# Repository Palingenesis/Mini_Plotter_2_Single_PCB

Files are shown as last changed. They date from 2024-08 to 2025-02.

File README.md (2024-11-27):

# This is My Mini Plotter 2 with a Single PCB  
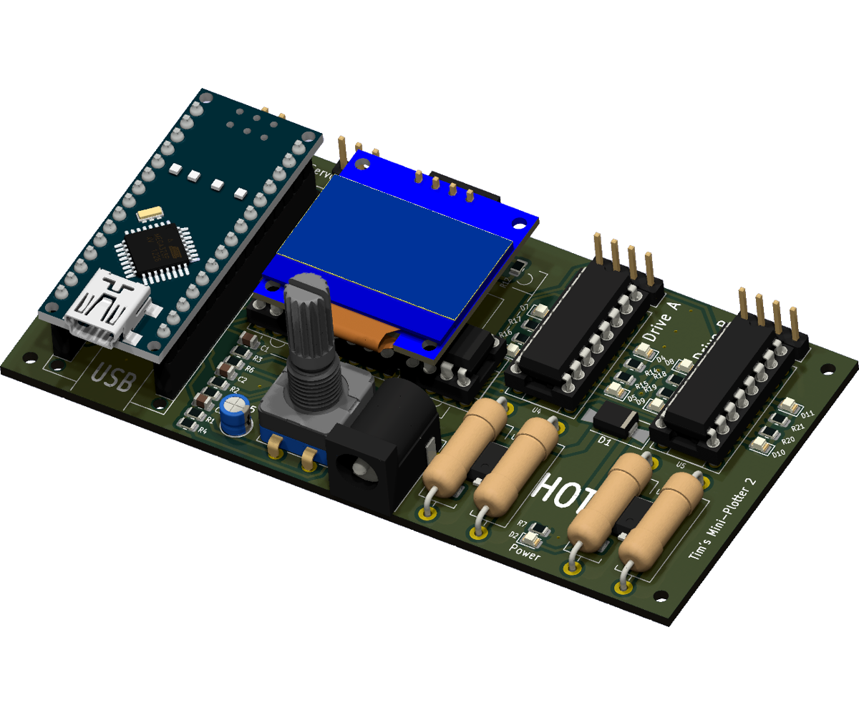
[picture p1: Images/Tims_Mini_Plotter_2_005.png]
  
## This is a Board to control two basic bipolar stepper motors.  
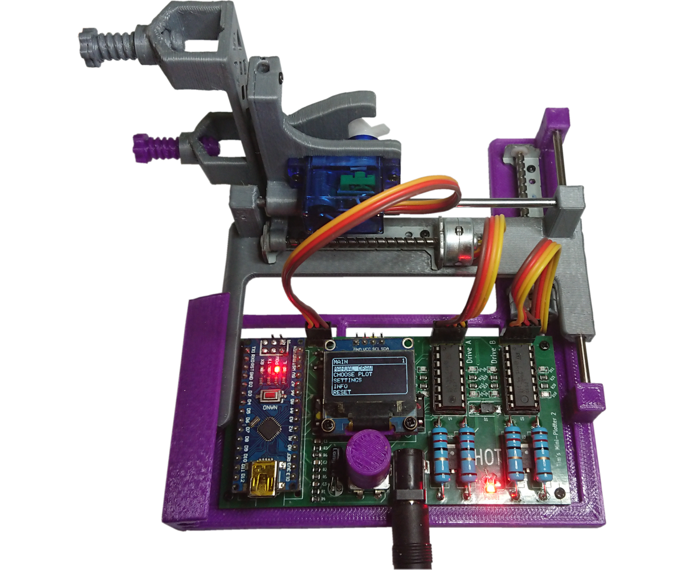
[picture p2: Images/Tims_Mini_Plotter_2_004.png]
Mini Plotter
  
## *The Board fitted to the Mini Plotter.*  
### Files for [KiCAD EDA](https://www.kicad.org/)  
There is [<span style="font-size: large;">**"Mini Plotter 2 Full.kicad_pcb.zip"**</span>](bom/) file  
* This can be used when **"Plot Files"** asked for at 
<sub></sub> 
when ordering 10 PCBs for $5  
* If you have <span style="font-size: large;">**[KiCAD EDA](https://www.kicad.org/)**</span>,  
<sub></sub>
have a Plugin Plugin that will make things simple to order a PCB,  
just load this project into <span style="font-size: large;">**[KiCAD EDA](https://www.kicad.org/)**</span> install the plugin click the Icon Plugin and it will create all the nesesery files needed and take you to order a PCB 
and compeate the form on 
<sub></sub> 
web site.  
  
<a href="https://www.pcbway.com/project/shareproject/Tim_s_Mini_Plotter_2_ec46c4f8.html">PCB from PCBWay</a>

### Files for [3D Printing](https://www.pcbway.com/rapid-prototyping/manufacture/?type=2&reffercode=TOP)  
There is [a folder with all the STL files needed](STL/) to print the Mini Plotter.

## Note!
The BOM only contains the Components for the Board.  
Other Parts required are:  
* Arduino Nano Module.
* 2 Stepper Motor 15mm dia. x 50mm Screw. (The type from CD or DVD drive)
* SG90 Servo.
* 3 lengths of 3mm Linear Rod.
* A light Spring 3mm x 25mm.
* 11 M1.7 x 6mm self tap flat nose screws.
* The 3D printed parts.
## About  
This is a PCBWay PCB Version of mini plotter I did quit a while ago, my original mini plotter I made of standard modules I bought and a home made PCB.

Details of the original can be found at my Blog here: [Tim's Mini Plotter 2 (tims-mini-plotter2.blogspot.com)](https://tims-mini-plotter2.blogspot.com/2019/01/tims-mini-plotter-2-this-is-new-project.html)

So it is the PCBWay PCB version.  
PCBWay do a great offer in prototyping PCBs, so I decided to make a version based around a single PCB.  
This is the same as the original except for the electronics, it has been made slightly longer to accommodate a single PCB.
## My Brief
For this project, I wanted to make a compact portable plotter using 2 motors from CD/DVD Drives.  
I wanted to use the cheap L298 drivers.  
I wanted to give it some memory where it can store some plots, and have a menu system to set some basic settings and be able to chose plots stored in memory.
## What I use
I use [FreeCAD](https://www.freecad.org/)  to design my 3D Prints, and [KiCAD EDA](https://www.kicad.org/) to design my PCB.  
Both these programs can integrate with each other. They are open source and I recommend them.  
[KiCAD EDA](https://www.kicad.org/) also has a plugin Plugin from <sub></sub> that makes it simple to order PCBs.
## History
My previous Mini Plotter Ver. 1 looked like this: [Version 1](https://tims-mini-plotter-1.blogspot.com/) [Version 1.3](https://www.youtube.com/watch?v=I_yTPbJcGrc&feature=youtu.be)
### Here is is a video of the original Mini Plotter 2 to show how it works.
*Click this image to see a video of it in use.*
[](https://www.youtube.com/watch?v=dSBTWS-KP68)
This new version works exactly in the same way.
## Stepper Motors
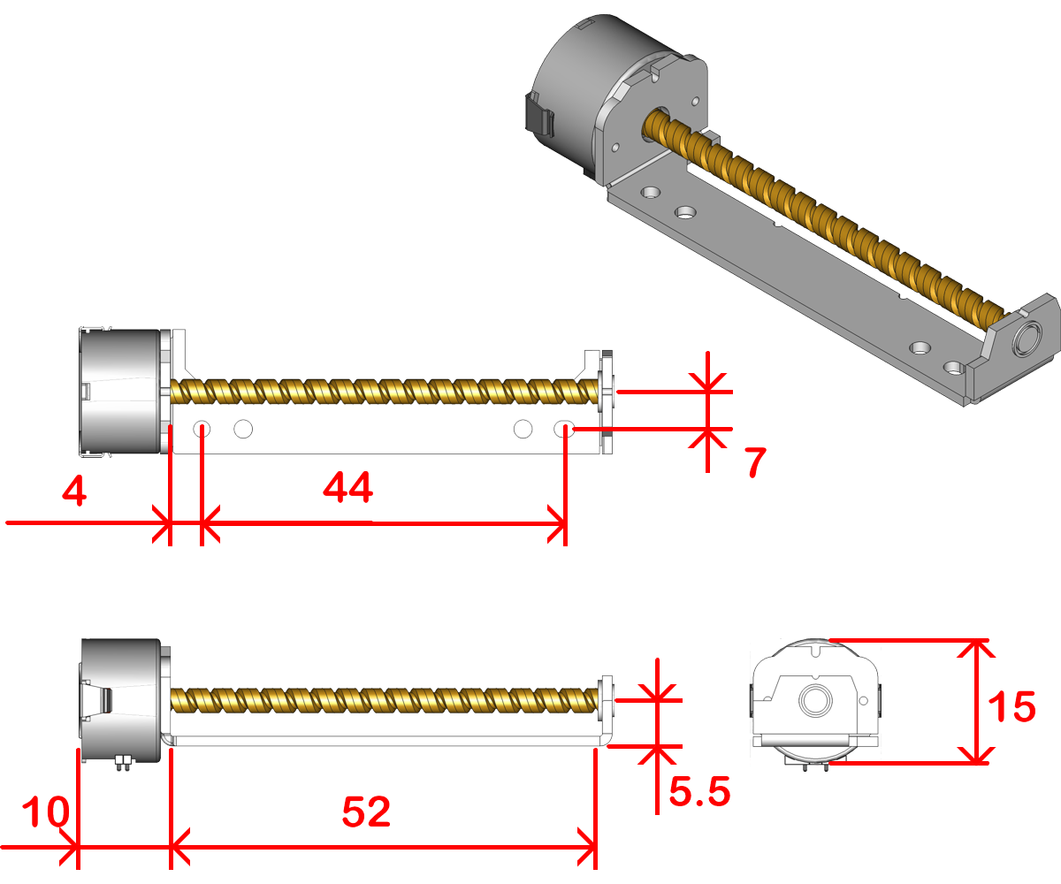
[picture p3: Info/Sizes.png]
  
The stepper motors I am using for this project are motors I repurposed from some CD/DVD drives.  
The dimensions are approximate, I have put holes to suit what I have shown.  
Care should be taken when soldering new cables to these motors, it is very easy to melt the coil bobbins.  
The only data I could find for these type of motors was from a data sheet for a PL15S-020. (I will assume other makes are similar)  
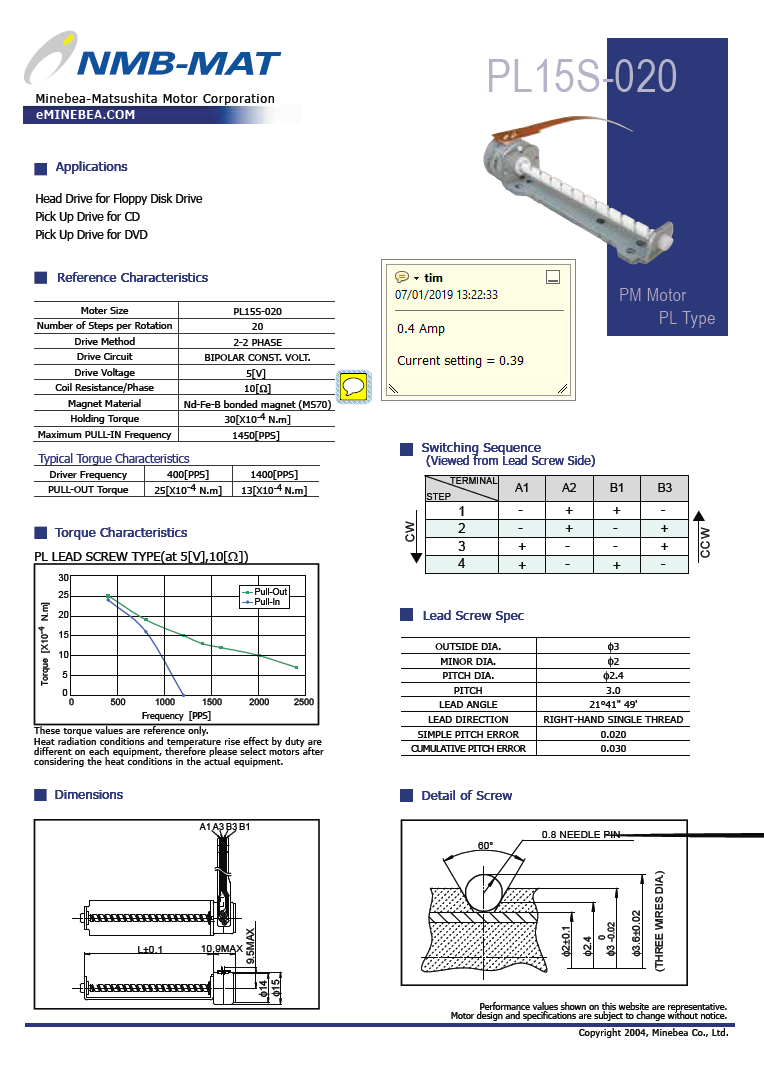
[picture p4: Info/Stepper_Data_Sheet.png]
  
If we do a little maths: V=ri, 5 volt divided by 10 ohms = 0.5 Amps  
As I could check the resistance of my motors and found them to have 12 ohm resistance.  
I will work on the assumption mine require 0.4A. (5/12=0.42A)  
They probably are designed to take 0.5A, but: they are normally mounted to a large metal frame that acts like a massive heat sink.  
My steppers are going to be mounted to plastic. (PLA)  
Knowing this I will be wiring the Voltage regulators in the Constant Current configuration. (see L78xx family data sheets)  
I had some 12.5 ohm 2 Watt Resistors, so I have 2 for each drive.  
12.5 ohm 2 Watt two in parallel making 6.25 ohm.  
## Motor Driver
I have used two L293 drivers to drive the stepper motors.  
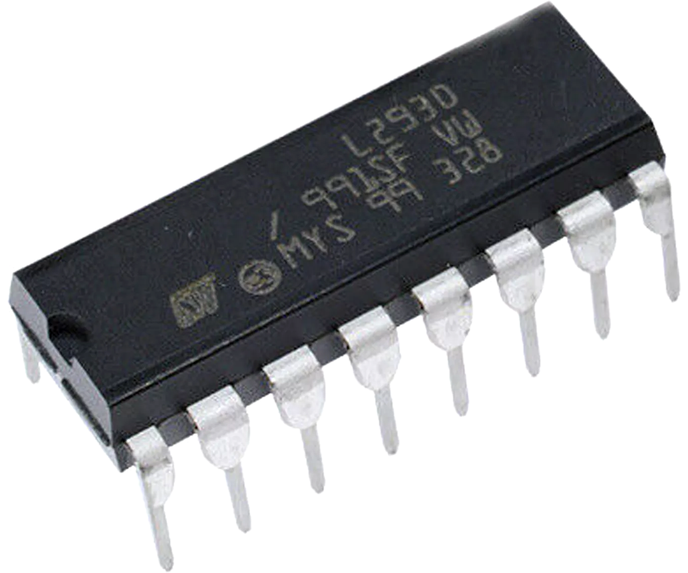
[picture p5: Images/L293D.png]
  
## Memory
I have used two 24C256 I2C Memory Chips, there is room for three.  
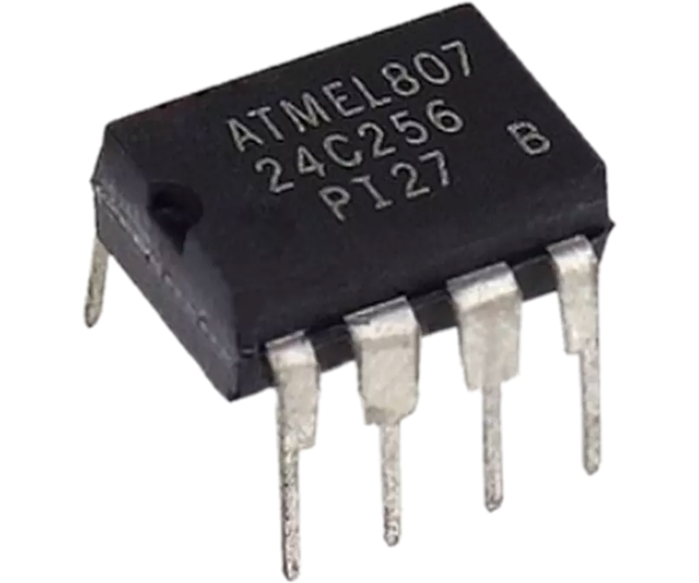
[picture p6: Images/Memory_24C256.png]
  
To program the memory you will need the Application I wrote and some Arduino code.  
I have gone into detail of how I compress G-Code command lines to 3 bytes on my blog here: [Adding Memory to Arduino NANO and compressing G-Code (tims-mini-plotter2.blogspot.com)](https://tims-mini-plotter2.blogspot.com/2019/04/adding-memory-to-arduino-nano-and.html)  
## Servo
The servo is any SG90.  
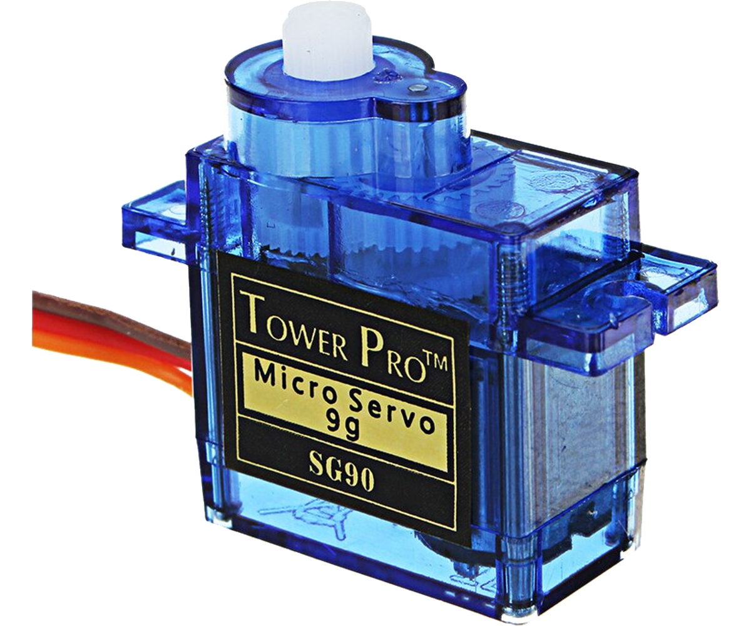
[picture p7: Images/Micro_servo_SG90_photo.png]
  
The horn I used had two long and two short arms.  
## Display
The display is an I2C 0.9 inch OLED  
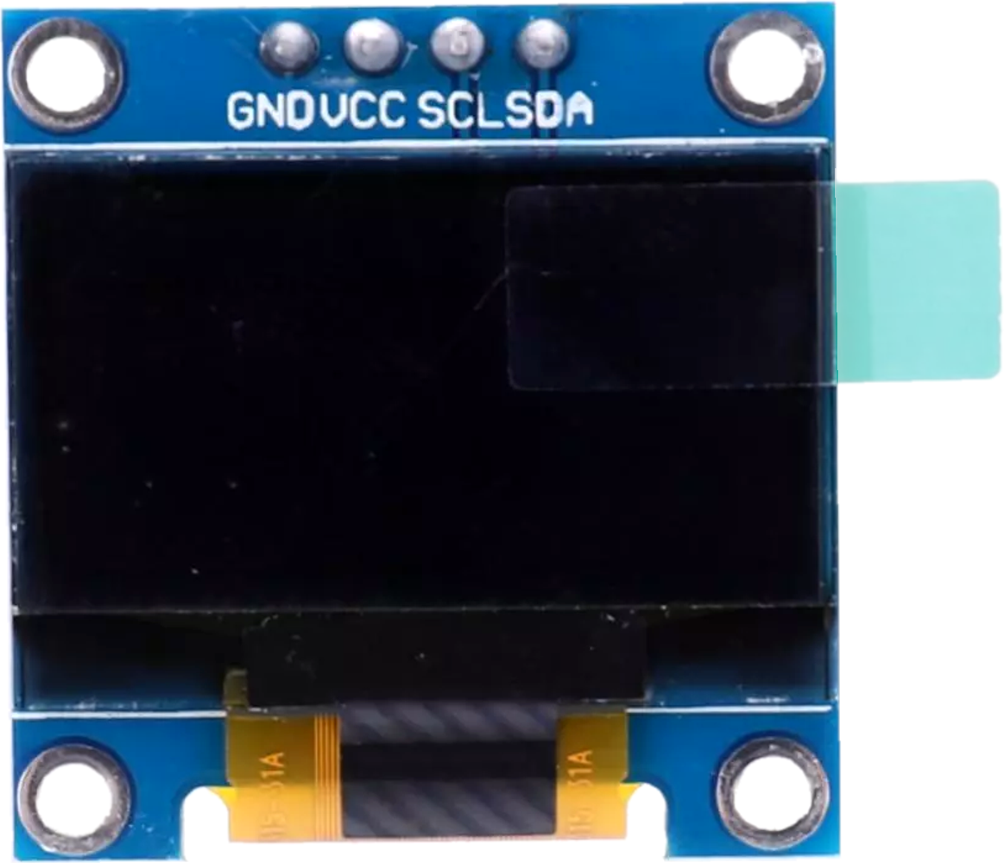
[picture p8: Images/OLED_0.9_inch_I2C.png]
  
## Power
I have added the L7805 to power the servo or a laser.  
Any 5v auxiliary device can be attached to this switched output.  
The Arduino Nano has its own Linear regulator, this regulator limits the input voltage to 12v. (I should have wired it differently)  
The plotter runs best above 10 Volts.  
## Assembly Of the Plotter.
Assembly is the same as I did with the original here: [Tim's Mini Plotter 2: Assembly (tims-mini-plotter2.blogspot.com)](https://tims-mini-plotter2.blogspot.com/2019/03/assembly.html)  
The only difference is the parts use.  
* There is a [folder of Images ](Assembly_Images/) that show how these parts go to gether.  
* As I mentioned, this is modified to take the new Single PCB by <sub></sub>.  
* Please read some of the original Blog, There are things that need attention. The Screw Pad, The Linear Rod Fit.  
## Instructable.  
I have also done an Instructable of the new version.  
[Tim's Mini Plotter 2 With Single PCB](https://www.instructables.com/Tims-Mini-Plotter-2-With-Single-PCB/)  
## I did some Live Streams should you want to make this.
These are the sort of stream you click through to find the info you want.  
Treat them like a reference book. :)    
[Tim Live Part 1 of Mini Plotter (youtube.com)](https://www.youtube.com/watch?v=YSE00Mr2BqY)  
[Tim Live Part 2 of Mini Plotter (youtube.com)](https://www.youtube.com/watch?v=kGypXZ9P3tI&t=1s)  
[Tim Live Part 3 of Mini Plotter (youtube.com)](https://www.youtube.com/watch?v=wI7Unksa26g&t=3s)

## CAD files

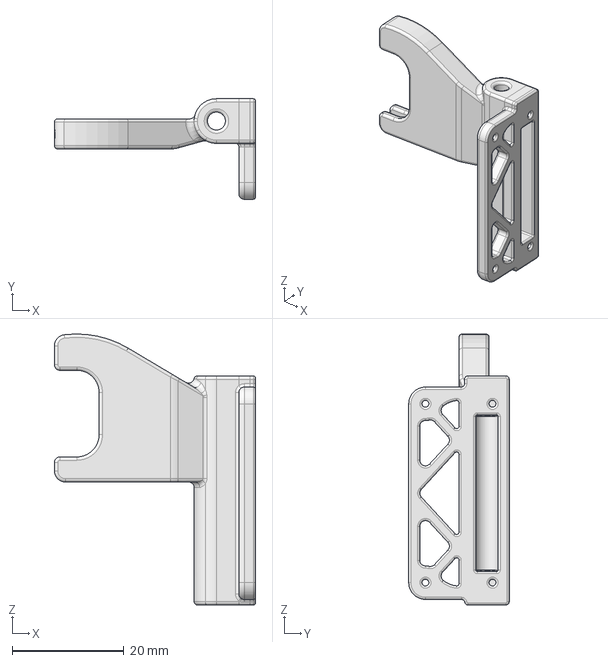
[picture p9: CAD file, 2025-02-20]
FreeCAD/Part Z.FCStd
36.0 x 18.0 x 48.5 mm

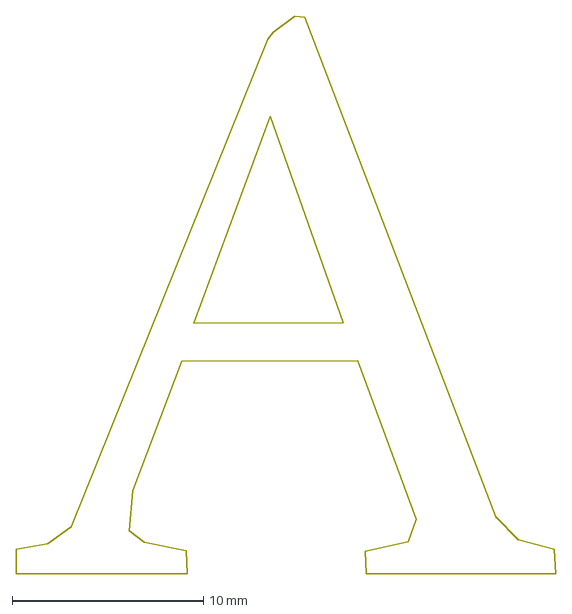
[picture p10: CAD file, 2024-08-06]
Memory_Package/TGC/Capitals/A.dxf
28.2 x 29.1 mm

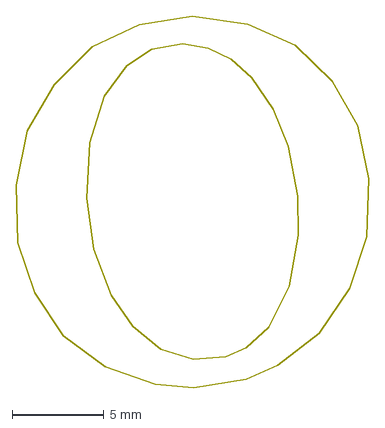
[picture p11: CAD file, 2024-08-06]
Memory_Package/TGC/Lower Case/o_.dxf
19.2 x 20.2 mm

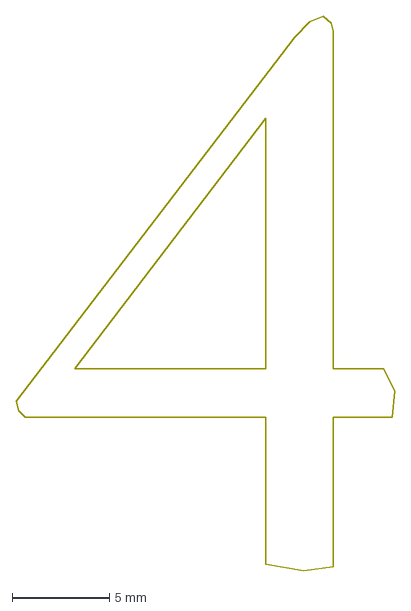
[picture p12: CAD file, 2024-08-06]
Memory_Package/TGC/Numbers/4.dxf
19.4 x 28.5 mm

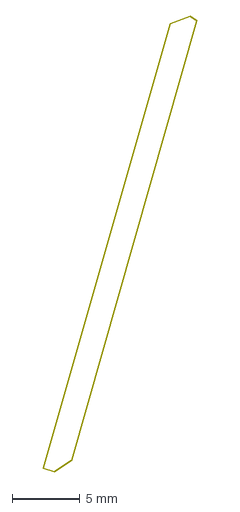
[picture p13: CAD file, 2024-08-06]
Memory_Package/TGC/Symbols/Char_47.dxf
11.4 x 33.7 mm

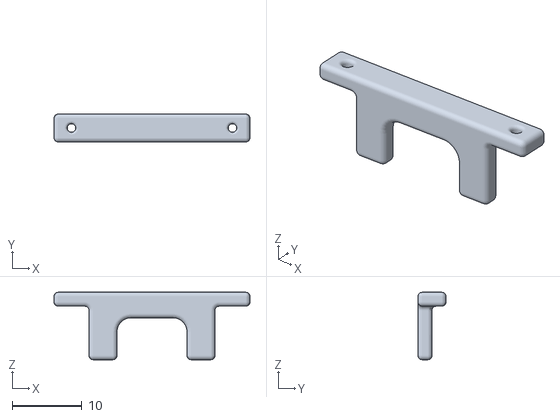
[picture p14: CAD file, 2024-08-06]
STL/OLED_Support.stl
28.0 x 4.00 x 9.65

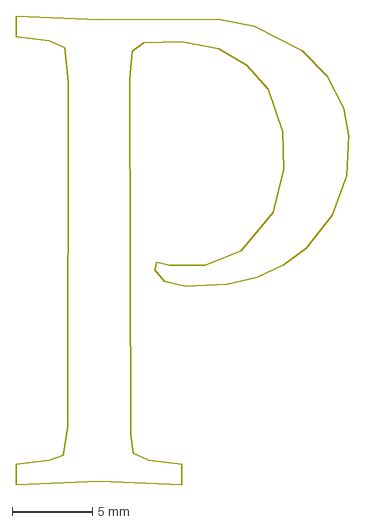
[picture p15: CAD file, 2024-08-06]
Memory_Package/TGC/Capitals/P.dxf
20.7 x 29.2 mm

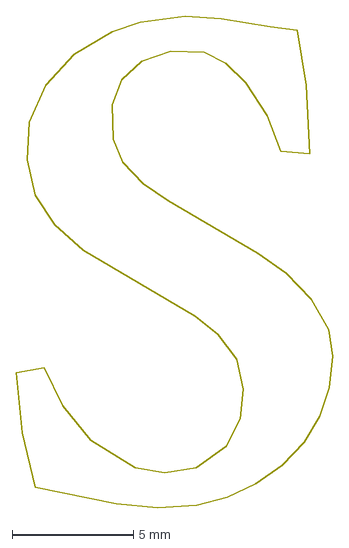
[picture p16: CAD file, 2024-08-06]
Memory_Package/TGC/Lower Case/s_.dxf
13.0 x 20.3 mm

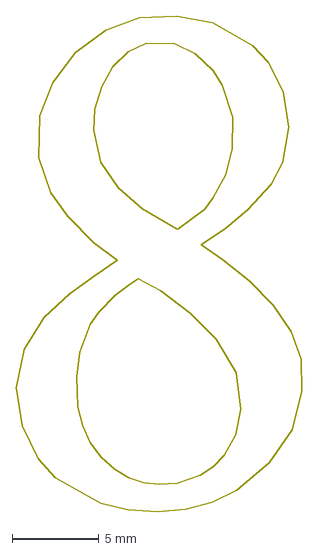
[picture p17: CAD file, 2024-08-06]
Memory_Package/TGC/Numbers/8.dxf
16.5 x 28.6 mm

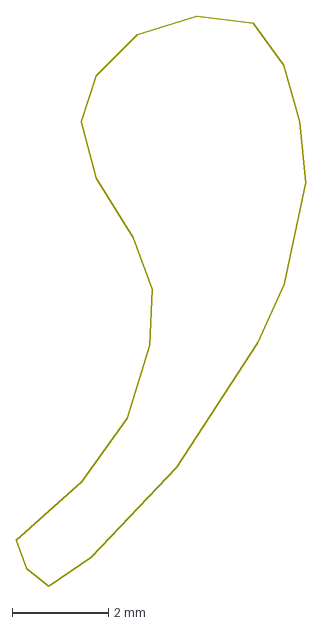
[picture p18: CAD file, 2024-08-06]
Memory_Package/TGC/Symbols/Char_44.dxf
6.02 x 11.8 mm

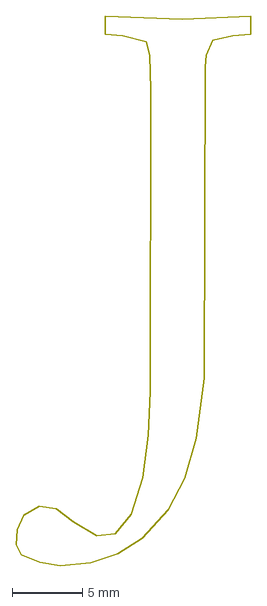
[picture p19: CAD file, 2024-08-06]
Memory_Package/TGC/Capitals/J.dxf
16.6 x 39.0 mm

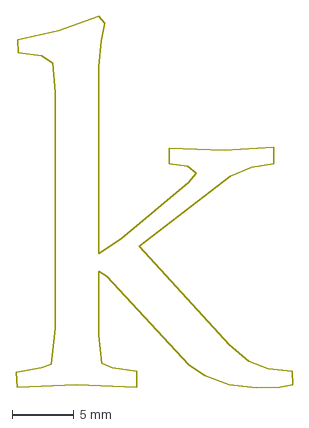
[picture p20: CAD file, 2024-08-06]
Memory_Package/TGC/Lower Case/k_.dxf
22.3 x 30.0 mm

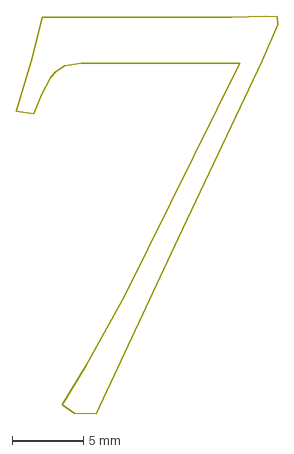
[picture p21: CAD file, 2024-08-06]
Memory_Package/TGC/Numbers/7.dxf
18.4 x 28.0 mm

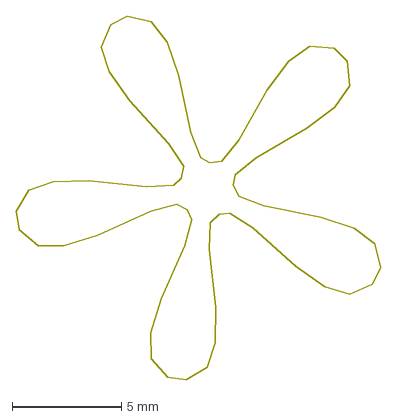
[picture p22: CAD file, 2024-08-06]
Memory_Package/TGC/Symbols/Char_42.dxf
16.6 x 16.6 mm

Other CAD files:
STL/Knob.stl
Memory_Package/TGC/Capitals/O.dxf
Memory_Package/TGC/Lower Case/a_.dxf
Memory_Package/TGC/Numbers/3.dxf
Memory_Package/TGC/Capitals/B.dxf
Memory_Package/TGC/Capitals/C.dxf
Memory_Package/TGC/Capitals/D.dxf
Memory_Package/TGC/Capitals/E.dxf
Memory_Package/TGC/Capitals/F.dxf
Memory_Package/TGC/Capitals/G.dxf
Memory_Package/TGC/Capitals/H.dxf
Memory_Package/TGC/Capitals/I.dxf
Memory_Package/TGC/Capitals/K.dxf
Memory_Package/TGC/Capitals/L.dxf
Memory_Package/TGC/Capitals/M.dxf
Memory_Package/TGC/Capitals/N.dxf
Memory_Package/TGC/Capitals/Q.dxf
Memory_Package/TGC/Capitals/R.dxf
Memory_Package/TGC/Capitals/S.dxf
Memory_Package/TGC/Capitals/T.dxf
Memory_Package/TGC/Capitals/U.dxf
Memory_Package/TGC/Capitals/V.dxf
Memory_Package/TGC/Capitals/W.dxf
Memory_Package/TGC/Capitals/X.dxf
Memory_Package/TGC/Capitals/Y.dxf
Memory_Package/TGC/Capitals/Z.dxf
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

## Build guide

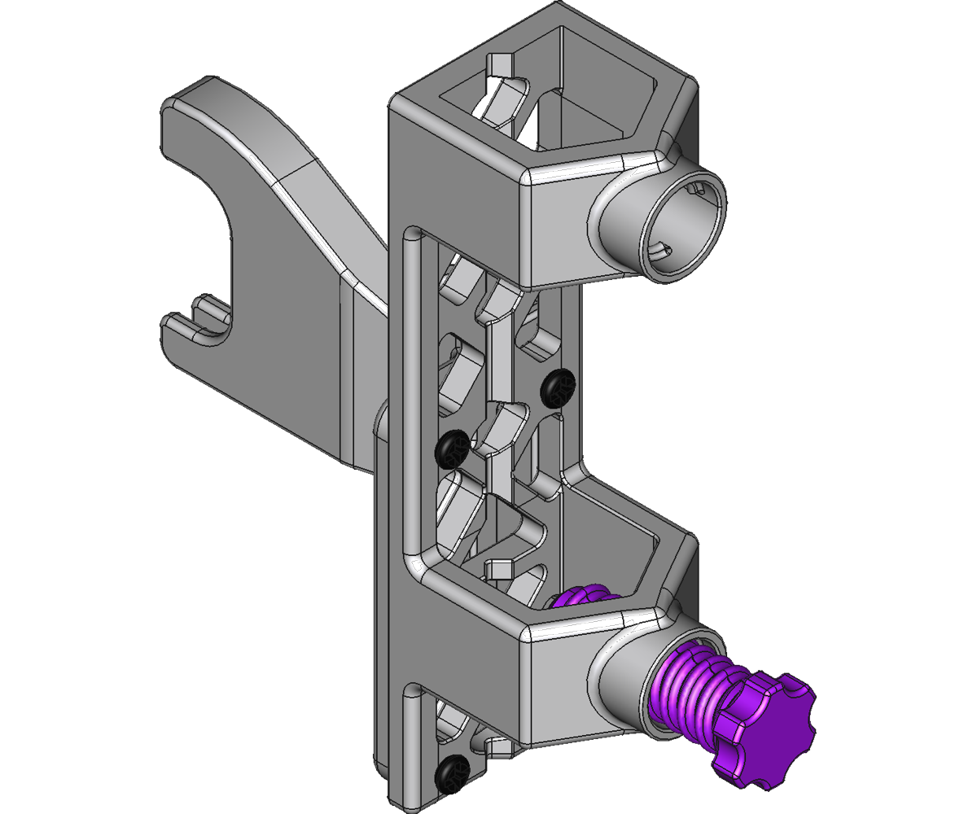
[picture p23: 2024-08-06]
Assembly_Images/Mini_Plotter_With_New_PCB 006.png

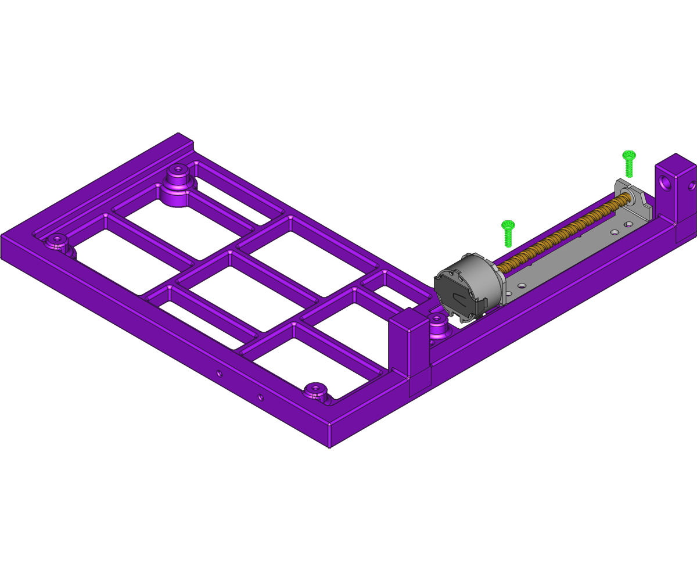
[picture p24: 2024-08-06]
Assembly_Images/Mini_Plotter_With_New_PCB 001.png

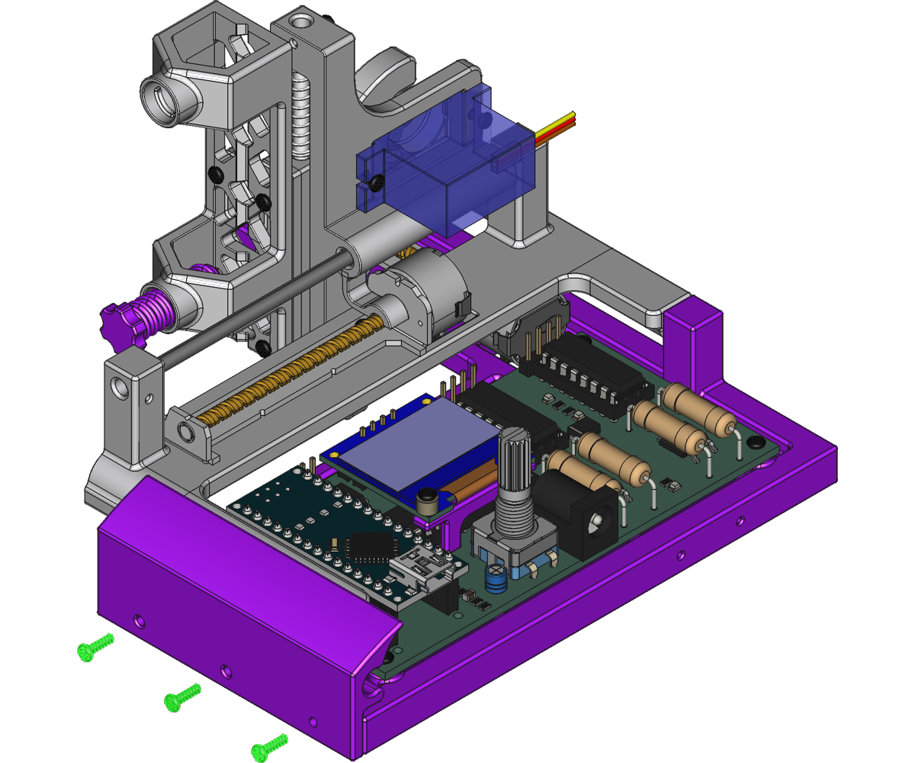
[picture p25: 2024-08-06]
Assembly_Images/Mini_Plotter_With_New_PCB 013.png

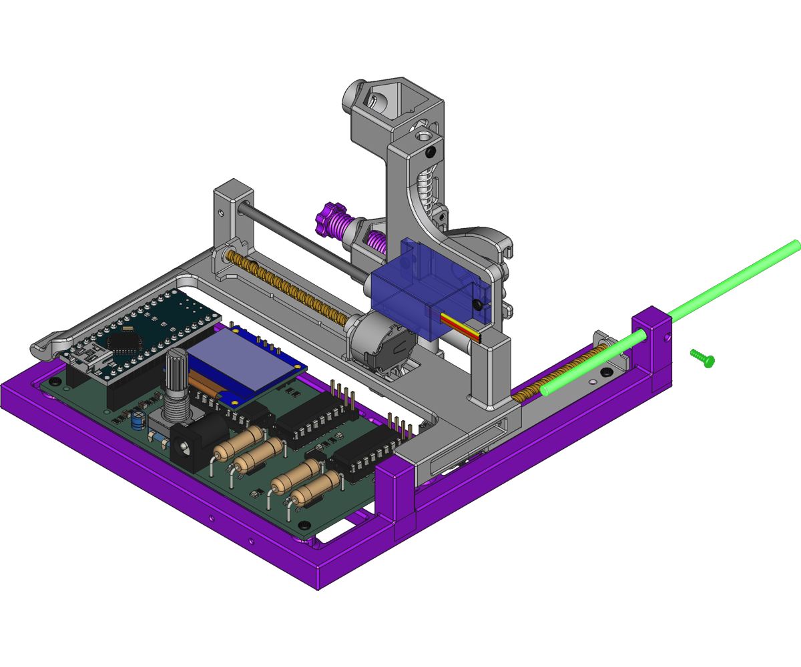
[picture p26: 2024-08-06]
Assembly_Images/Mini_Plotter_With_New_PCB 011.png

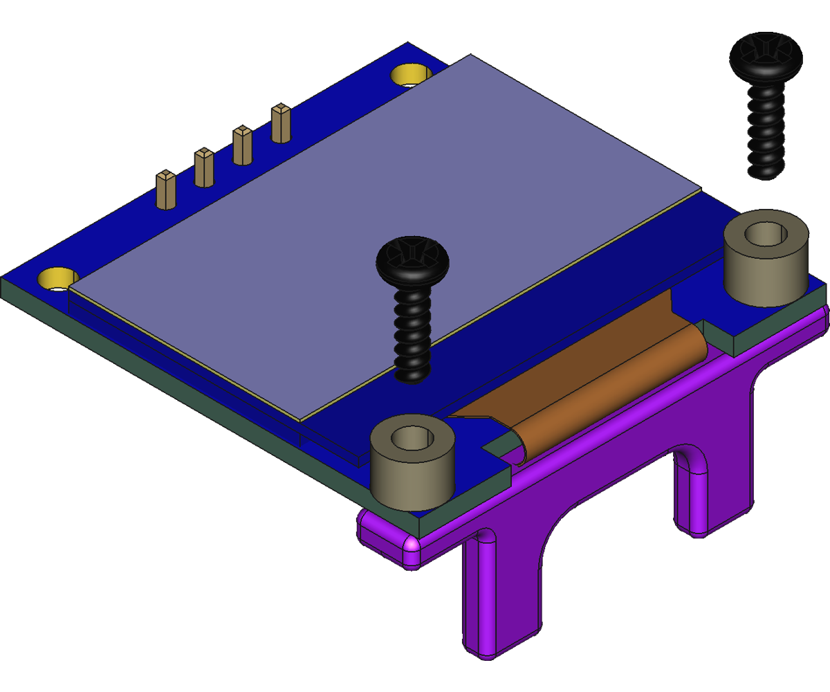
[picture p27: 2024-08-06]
Assembly_Images/Mini_Plotter_With_New_PCB 017.png

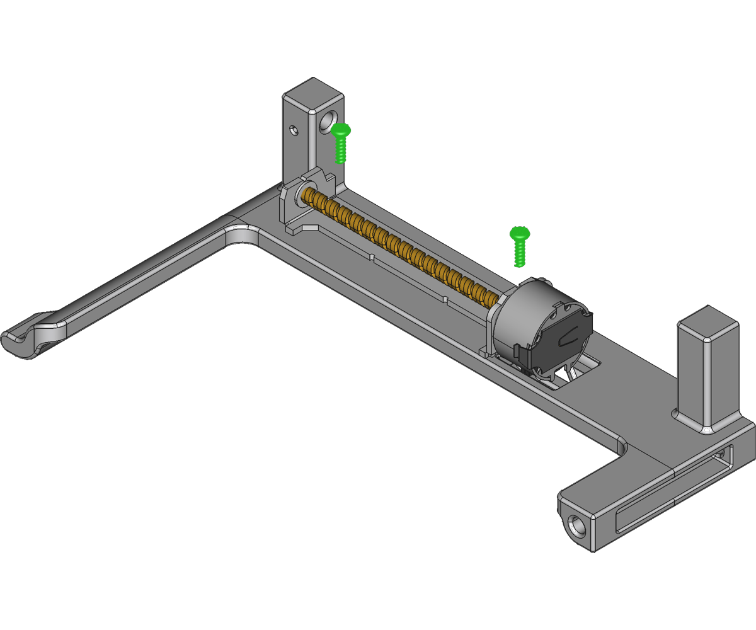
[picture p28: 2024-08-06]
Assembly_Images/Mini_Plotter_With_New_PCB 003.png

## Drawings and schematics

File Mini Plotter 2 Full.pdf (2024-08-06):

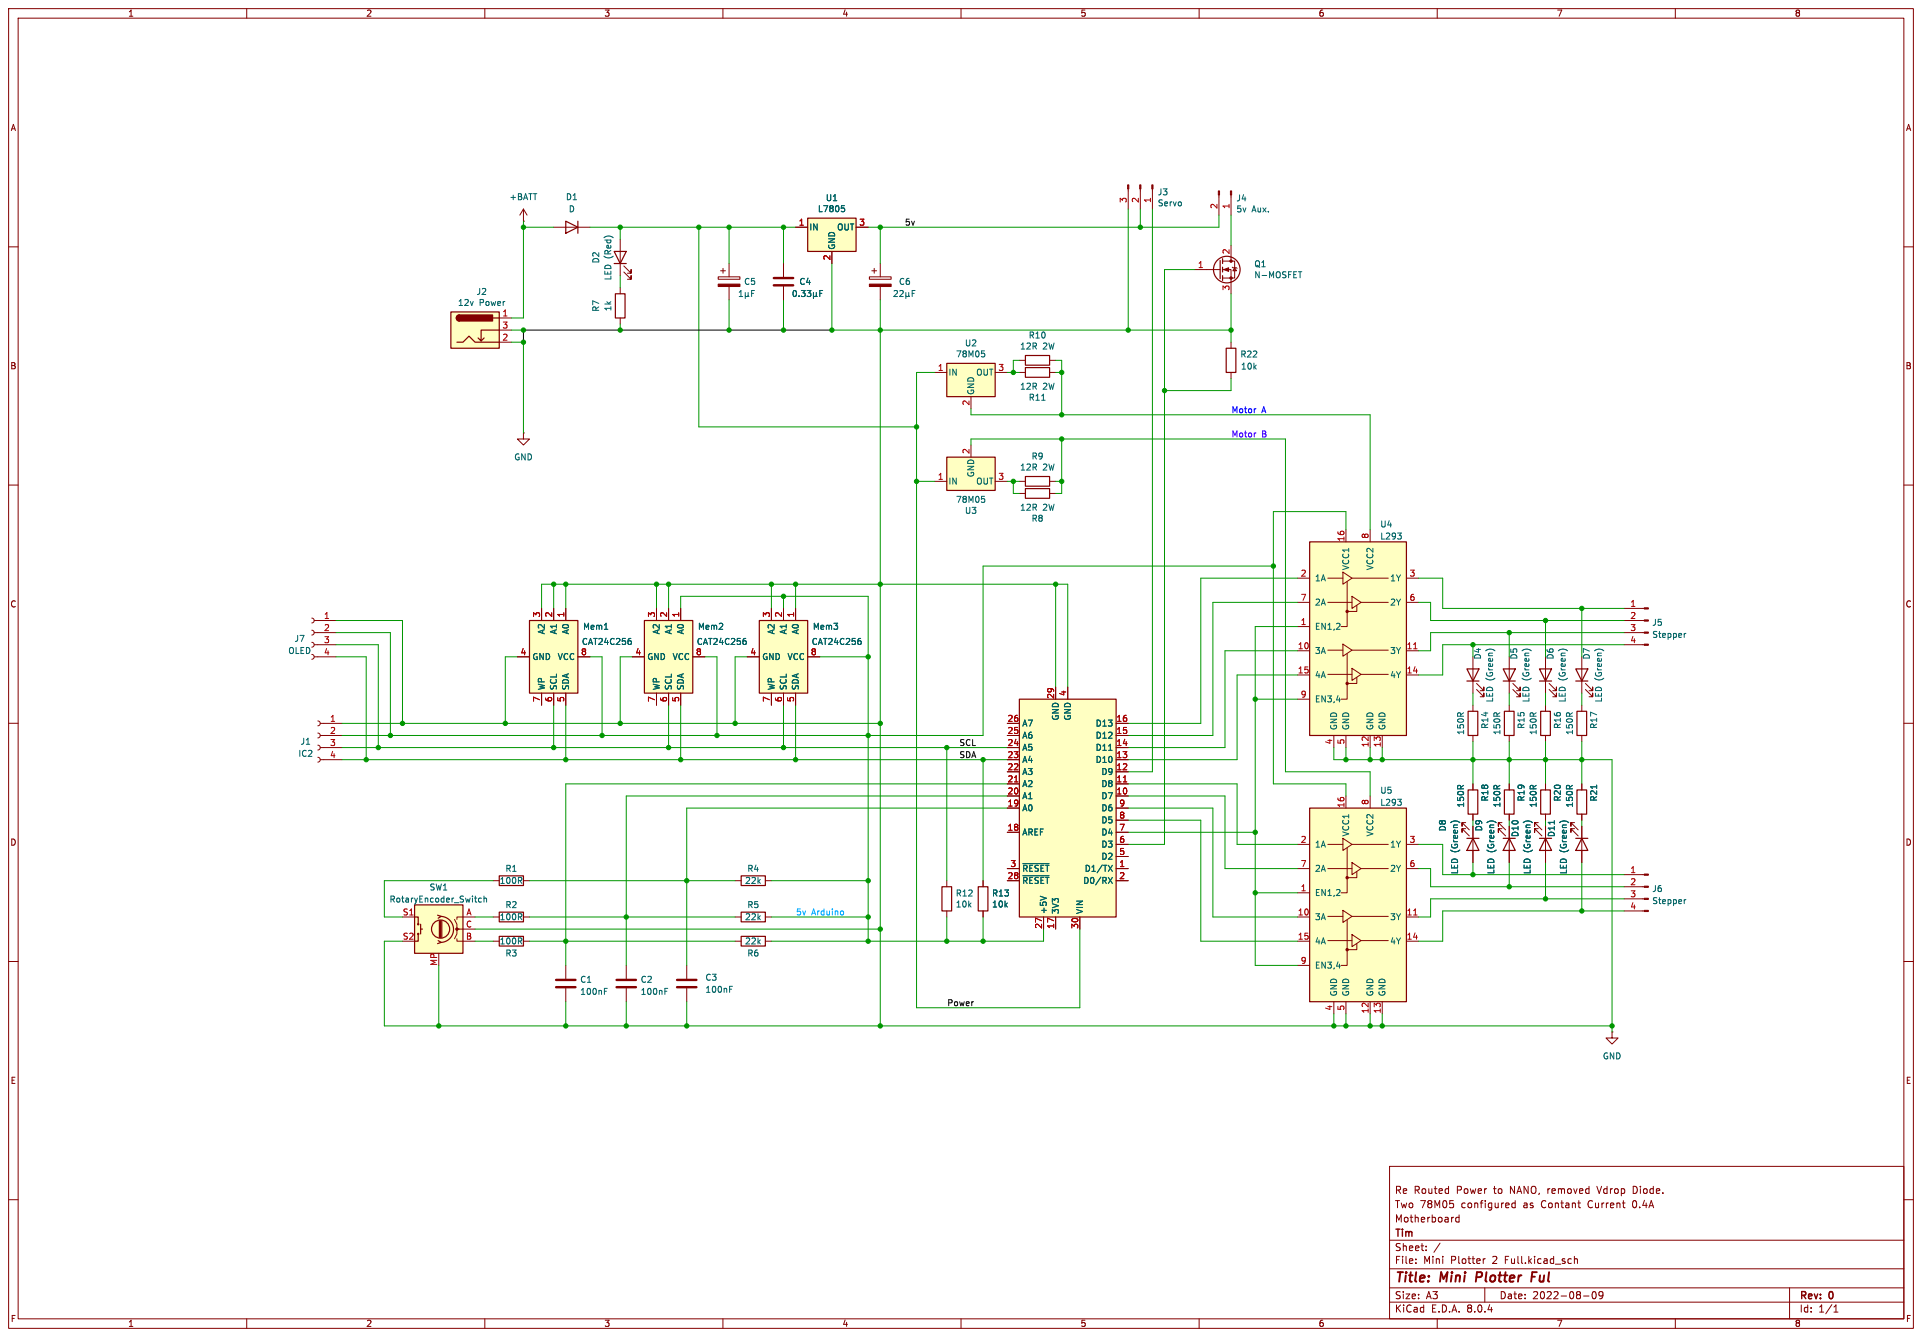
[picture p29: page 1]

2 OUT 3 D10 LED (Green) R21 150R D11 LED (Green) R20 150R R19 150R R18 150R D9 LED (Green) D8 LED (Green)

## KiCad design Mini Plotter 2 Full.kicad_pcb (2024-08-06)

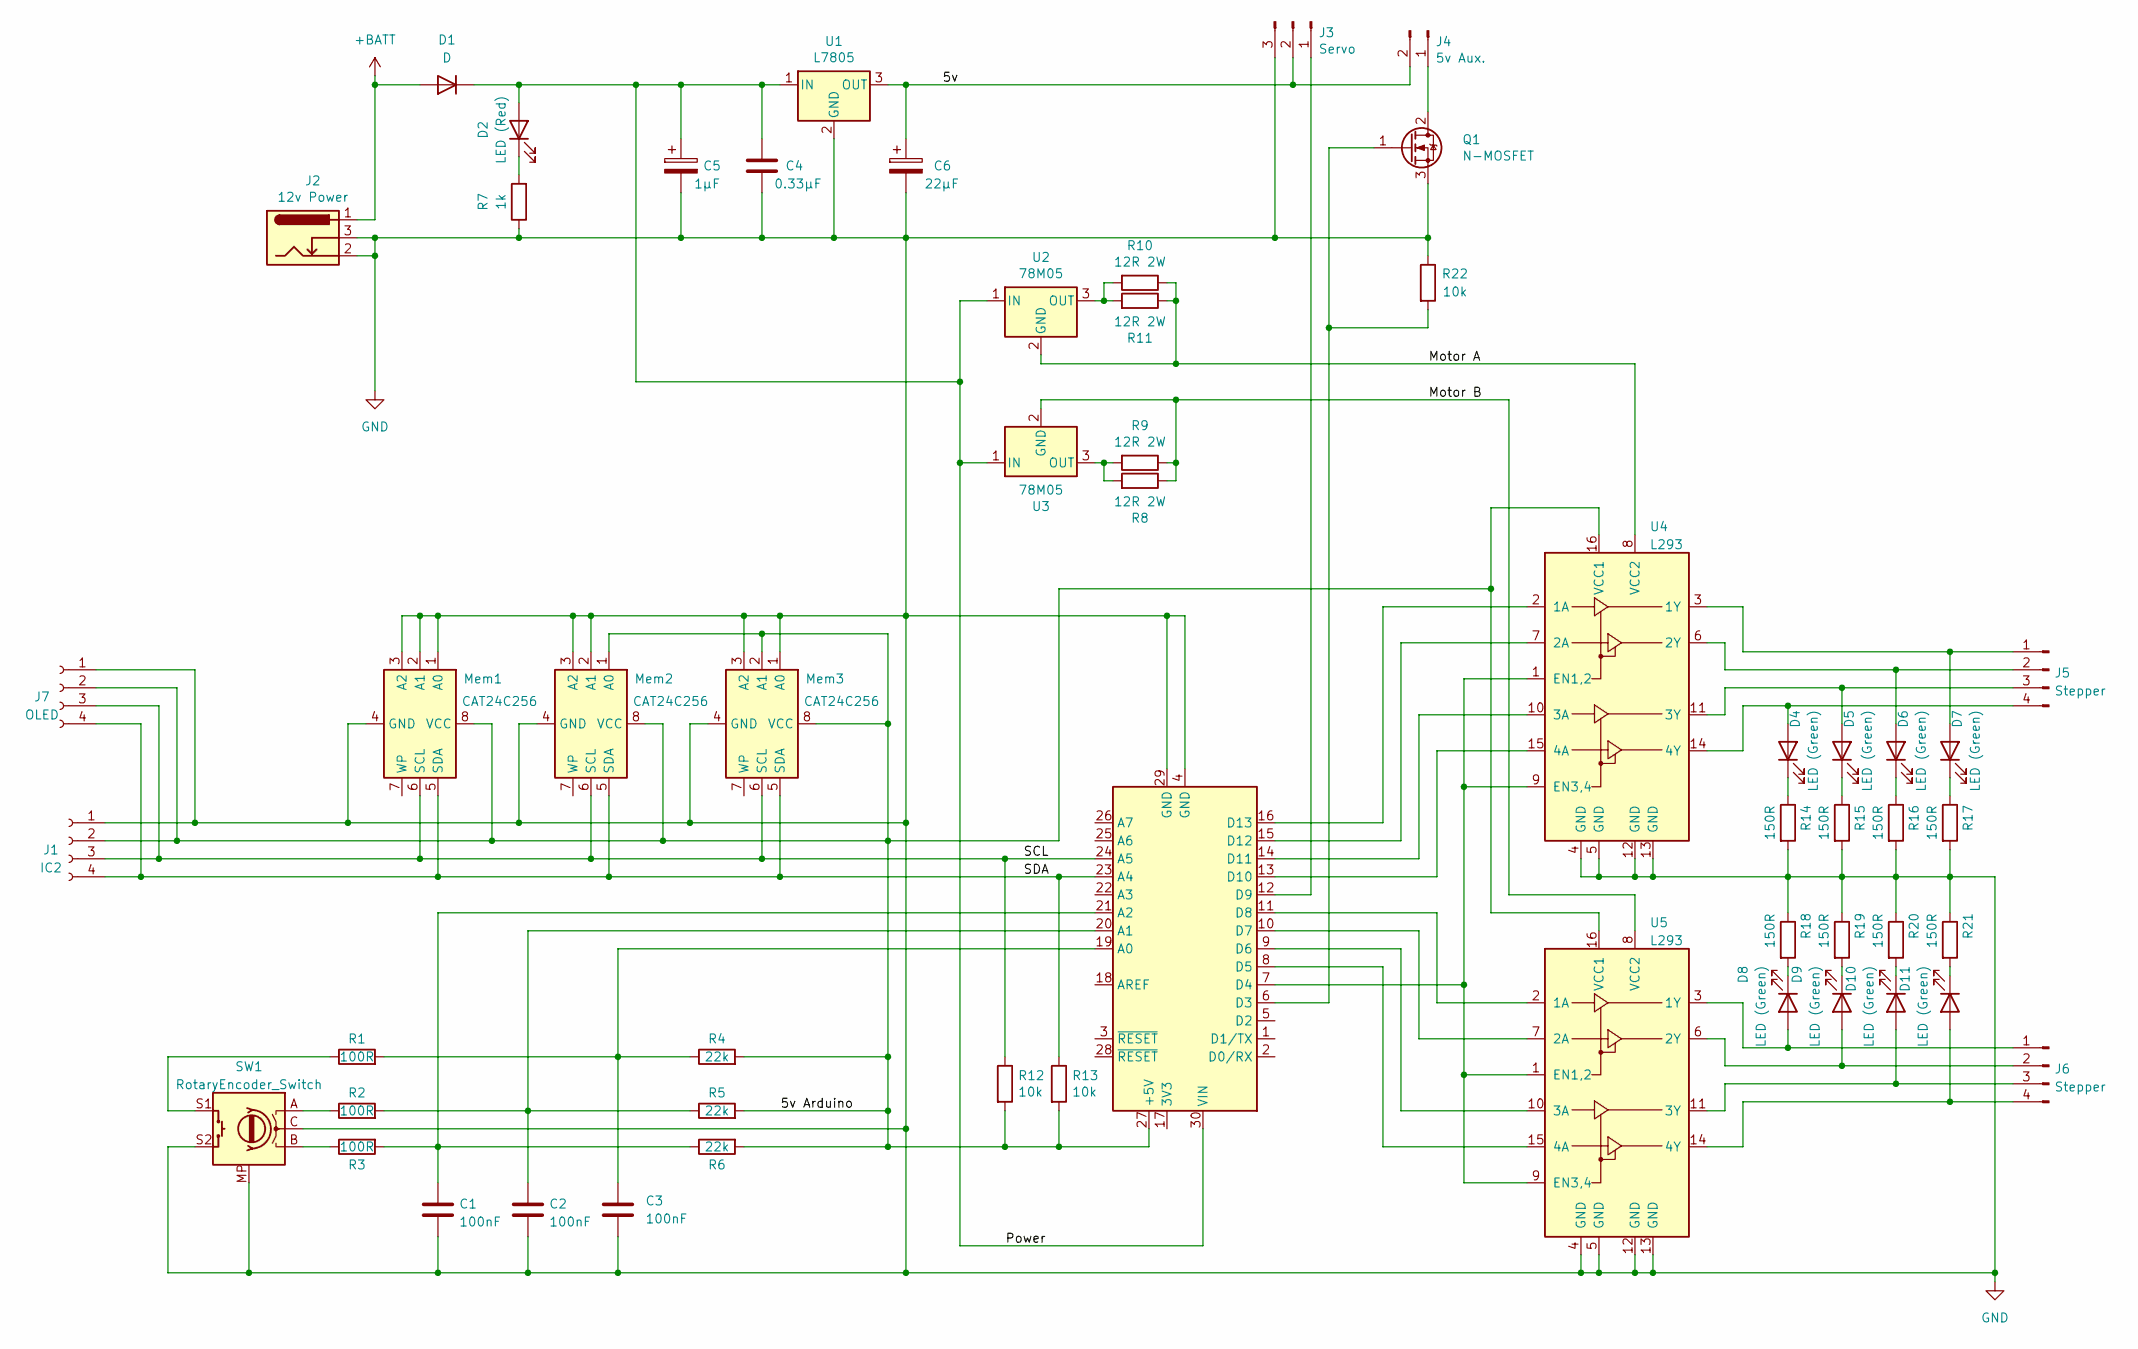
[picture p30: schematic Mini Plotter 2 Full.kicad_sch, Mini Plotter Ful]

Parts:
A1: Arduino_Nano_v3.x; Arduino_Nano_WithMountingHoles
C1, C2, C3: 100nF; C_0805_2012Metric
C4: 0.33µF; C_0805_2012Metric
C5: 1µF; CP_Radial_D4.0mm_P2.00mm
C6: 22µF; CP_Radial_D4.0mm_P2.00mm
D1: D; D_SMA-SMB_Universal_Handsoldering
D2: LED (Red); LED_0805_2012Metric
D4, D5, D6, D7, D8, D9, D10, D11: LED (Green); LED_0805_2012Metric
J1: IC2; PinSocket_1x04_P2.54mm_Vertical
J2: 12v Power; BarrelJack_Horizontal
J3: Servo; PinHeader_1x03_P2.54mm_Vertical
J4: 5v Aux.; PinHeader_1x02_P2.54mm_Vertical
J5, J6: Stepper; PinHeader_1x04_P2.54mm_Vertical
J7: OLED; OLED_I2C_096in_Module
Mem1, Mem2, Mem3: CAT24C256; DIP-8_W7.62mm_Socket
Q1: N-MOSFET; TO-252-3_TabPin2
R1, R2, R3: 100R; R_0805_2012Metric
R4, R5, R6: 22k; R_0805_2012Metric
R7: 1k; R_0805_2012Metric
R8, R9, R10, R11: 12R 2W; R_Axial_DIN0516_L15.5mm_D5.0mm_P20.32mm_Horizontal
R12, R13, R22: 10k; R_0805_2012Metric
R14, R15, R16, R17, R18, R19, R20, R21: 150R; R_0805_2012Metric
SW1: RotaryEncoder_Switch; RotaryEncoder_Alps_EC11E-Switch_Vertical_H20mm
U1: L7805; TO-252-2
U2, U3: 78M05; TO-252-2
U4, U5: L293; DIP-16_W7.62mm_Socket

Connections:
+BATT: D1.2 (A), J2.1
/5v: C6.1, J3.2, J4.2, U1.3 (OUT)
/5v Arduino: A1.27 (+5V), J1.2, J7.2, Mem1.8 (VCC), Mem2.1 (A0), Mem2.8 (VCC), Mem3.2 (A1), Mem3.8 (VCC), R4.2, R5.2, R6.2, R12.2, R13.2, U4.16 (VCC1), U5.16 (VCC1)
/Motor A: R10.1, R11.1, U2.2 (GND), U4.8 (VCC2)
/Motor B: R8.1, R9.1, U3.2 (GND), U5.8 (VCC2)
/Power: A1.30 (VIN), C4.1, C5.1, D1.1 (K), D2.2 (A), U1.1 (IN), U2.1 (IN), U3.1 (IN)
/SCL: A1.24 (A5), J1.3, J7.3, Mem1.6 (SCL), Mem2.6 (SCL), Mem3.6 (SCL), R12.1
/SDA: A1.23 (A4), J1.4, J7.4, Mem1.5 (SDA), Mem2.5 (SDA), Mem3.5 (SDA), R13.1
GND: A1.4 (GND), A1.29 (GND), C1.2, C2.2, C3.2, C4.2, C5.2, C6.2, J1.1, J2.2, J2.3, J3.3, J7.1, Mem1.1 (A0), Mem1.2 (A1), Mem1.3 (A2), Mem1.4 (GND), Mem2.2 (A1), Mem2.3 (A2), Mem2.4 (GND), Mem3.1 (A0), Mem3.3 (A2), Mem3.4 (GND), Q1.3 (S), R7.1, R14.2, R15.2, R16.2, R17.2, R18.1, R19.1, R20.1, R21.1, R22.1, SW1.C, SW1.MP (Case), SW1.S2, U1.2 (GND), U4.4 (GND), U4.5 (GND), U4.12 (GND), U4.13 (GND), U5.4 (GND), U5.5 (GND), U5.12 (GND), U5.13 (GND)
unnamed: A1.19 (A0), C3.1, R1.2, R4.1
unnamed: A1.20 (A1), C2.1, R2.2, R5.1
unnamed: A1.21 (A2), C1.1, R3.2, R6.1
unnamed: A1.6 (D3), Q1.1 (G), R22.2
unnamed: A1.7 (D4), U4.1 (EN1,2), U4.9 (EN3,4), U5.1 (EN1,2), U5.9 (EN3,4)
unnamed: A1.8 (D5), U5.15 (4A)
unnamed: A1.9 (D6), U5.10 (3A)
unnamed: A1.10 (D7), U5.7 (2A)
unnamed: A1.11 (D8), U5.2 (1A)
unnamed: A1.12 (D9), J3.1
unnamed: A1.13 (D10), U4.15 (4A)
unnamed: A1.14 (D11), U4.10 (3A)
unnamed: A1.15 (D12), U4.7 (2A)
unnamed: A1.16 (D13), U4.2 (1A)
unnamed: D2.1 (K), R7.2
unnamed: D4.2 (A), J5.4, U4.14 (4Y)
unnamed: D4.1 (K), R14.1
unnamed: D5.2 (A), J5.3, U4.11 (3Y)
unnamed: D5.1 (K), R15.1
unnamed: D6.2 (A), J5.2, U4.6 (2Y)
unnamed: D6.1 (K), R16.1
unnamed: D7.2 (A), J5.1, U4.3 (1Y)
unnamed: D7.1 (K), R17.1
unnamed: D8.2 (A), J6.1, U5.3 (1Y)
unnamed: D8.1 (K), R18.2
unnamed: D9.2 (A), J6.2, U5.6 (2Y)
unnamed: D9.1 (K), R19.2
unnamed: D10.2 (A), J6.3, U5.11 (3Y)
unnamed: D10.1 (K), R20.2
unnamed: D11.2 (A), J6.4, U5.14 (4Y)
unnamed: D11.1 (K), R21.2
unnamed: J4.1, Q1.2 (D)
unnamed: R1.1, SW1.S1
unnamed: R2.1, SW1.A
unnamed: R3.1, SW1.B
unnamed: R10.2, R11.2, U2.3 (OUT)
unnamed: R8.2, R9.2, U3.3 (OUT)

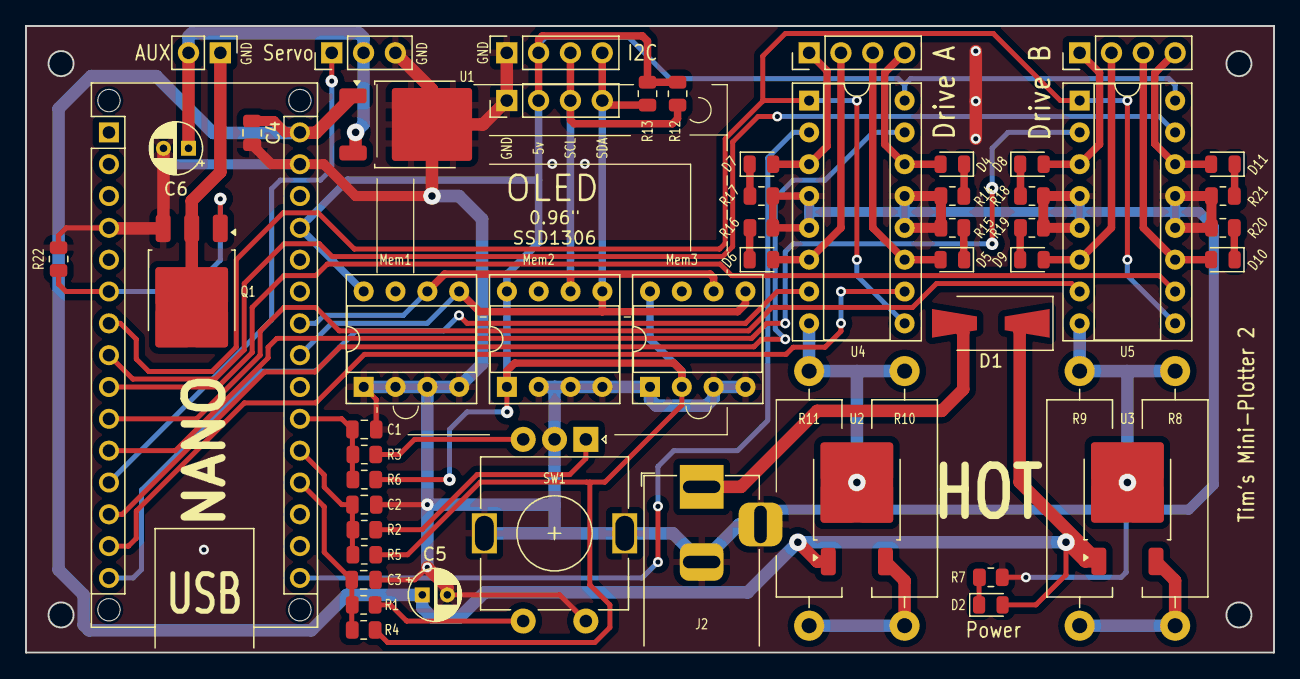
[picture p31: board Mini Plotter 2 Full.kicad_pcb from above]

Board: 2 copper layers, 99.6 x 50.0 mm, 56 parts (0 on the bottom side), 46 nets.

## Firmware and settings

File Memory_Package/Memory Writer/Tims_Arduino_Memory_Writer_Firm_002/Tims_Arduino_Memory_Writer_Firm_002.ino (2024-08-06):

/*
	Name:       Tims I2C Memory Writer Firmware
	Created:	27/02/2019 16:24:59
	Edited:		August 2024
	Author:     Tim Jackson.1960

	More info about this can be found at my Blog: https://tims-mini-plotter2.blogspot.com/2019/01/tims-mini-plotter-2-this-is-new-project.html
	Also the New version at: https://www.youtube.com/watch?v=YSE00Mr2BqY&t=1783s

	This is the bit of code I use to test and write data to 512 I2C EEPROM
	It has a sister program that is a windows aplication. https://drive.google.com/open?id=19ci9kac4xSghIvizUF5hXIfjpHqR-iEv
	It is code to store text as I ran out of memory on a NANO making a large menu system.


	Creadits:
		I have only used the Wire libray with this one. https://www.arduino.cc/

	ATMega328p (Arduino NANO)
	Sketch uses 6368 bytes (20%) of program storage space. Maximum is 30720 bytes.
	Global variables use 523 bytes (25%) of dynamic memory, leaving 1525 bytes for local variables. Maximum is 2048 bytes.


*/


#include <Wire.h>	/*	For I2C	*/

#define VERSION		1.1      /*	 My firmware version	*/
#define MAX_BUF		(64)     /*	 What is the longest message Arduino can store? The serial receive buffer holds 64 bytes.	*/
#define EEPROM_ADD	0x50    /*	 512 I2C EEPROM address (64k bytes) 	*/
#define MAX_I2C_PAGE_WRITE 64 

/*	SERIAL MESSAGES	*/
char  buffer[MAX_BUF];  /*	 message	*/
unsigned int no_data = 0;
unsigned int sofar;/*	 size of buffer	*/
bool procsessingString = false;
bool isSetting = false;

/*	MEMORY ADDRESSES	*/
char memWord[MAX_I2C_PAGE_WRITE];
byte memNumber = 0;
byte compData[3];
long MenuAddress = 0;/*	Mem 1 only	*/
long PlotNameAddress = 500;/*	Mem 1 only	*/
long dataStartAddress = 3000; /*	3000 for Mem 1, 0 for others.	*/
int lengthOfData = 3;


/*	WORDS USED IN MENUE and COMUNICATION (uses first mem chip, allocate first 500 bytes (0 to 499) to this)	*/
char* menuWords[] = { "MAIN", "MANUAL DRAW", "CHOOSE PLOT", "SETTINGS", "INFO", "RESET", "MOVE X", "DRAW X", "MOVE Y", "DRAW Y", "<<== BACK",
						"SPEED", "TOOL", "--", "Tim's Mini Plotter", "ok", "=== Motors Off ===", "Version: ", "Basic Gcode Commands",
						"M03 - Tool On/Down", "M05 - Tool Off/Up", "M18 - Motors Off", "System Reset", "M100 - this Info message",
						"R01 - Reset Plotter", "By Tim Jackson.1960", "================", "          ", "test A", "" };
int menuWordsLength = 29;

/*	 RULES FOR PLOT NAMES	*/

/*

	make all plot names 10 Characters to simplify menu system.
	will need 1 byte for Memory IC number. (needs to hold number 0 to 2)
	will need 2 bytes for start address. (needs to hold max number 32000)
	will need 2 bytes for length of plot data. (needs to hold max number 32000)

	Going to allocate 15 bytes to each plot.
	As I have managed to compress each command to 3 bytes, and I am using three 32k byte chips, I will probably have room for a lot of plots.
	So I am going to set aside the next 2500 bytes to the plot names. (500 to 2999)
	This is enough for 2500/15 = 166 plot names. (going to add the alphabet (74), abcdefghijklmnopqrstuvwxyxABCDEFGHIJKLMNOPQRSTUVWXYZ0123456789/*-+=()&%$£!)
	Actual plots will be a max of 92.

	As 166 plot names only use up to address 2990, I am going us 1 byte at address 2991 for storing the number of plot files saved. (needs to hold 0 to 166)

	I may alocate IC 3 to the alphabet at a later date after I see how it goes.

*/

/*	WORDS USED IN FILE MENU (old way i did it)*/
char* plotNames[] = { "Cube      ", "Snowflake ", "Wolf      ", "Links     ", "Witch     ", "Unicorn 1 ", "Butterfly ", "Spider    ", "Triangles ",
						"Skull     ", "Tim       ", "Alien     ", "Agent     ", "5 P Star  ", "9 P Star  ", "18 P Star ", "Reaper    ", "Octopus   " };
int plotNamesLength = 18;

void setup()
{
	Serial.begin(115200);	/*	 Initialize the serial	*/
	Wire.begin();
	Wire.setClock(400000);

	while (!Serial) {
		/*	 wait for serial port to connect.	*/
	}

	Serial.flush();
	Serial.println("Connected");
	delay(5);
	Serial.println("ok");
	Serial.flush();

	/*	 RULES TO STORE PLOTS	*/

	/*

		I2C Memory
		Total memory = 32k Bytes.
		Buffer = 64 Bytes.
		Write cycle time: 5ms

		Work out file system:
		1 char = 1 Byte.
		Lets make G-Code as short as posible.
		lets have only straight lines.
		No ARC commands.
		Have only up/off or down/on.

		Our max distance is 40mm.(actual max movement my plotter has is 42mm. but im rounding it for reasions.)
		But i want it to 1 decimal place.
		As bytes (8 bits) are are 0 to 255 positive numbers i will multiply our distance by 10, then divide it by 10 later.
		So the largest number is going to 409.
		I could use 2 bytes (16 bits) and have a max of 65,535 but I dont need that. I want to compress the code as mutch as posible.

		So I am going to convert things to the minimum bits needed.

		So max number = 409. 9 bits should hold that. (it will hold 511)
		We have 2 numbers so we need 2 of them, 18 bits so far.

		We need 1 bit to say if it is up/off or down/on

		That meens I only need 19 bits to make a command.
		as memory is stored in Bytes we are going to use 3 Bytes (24 bits). 5 bits won't be used.

		So standard G-Code:
		typical draw command = G01 X10.0 Y10.0 (this would normaly take up 15 Bytes of memory)
		typical move command = G00 X10.0 Y10.0 (this would normaly take up 15 Bytes of memory)

		So:
		up/off or down/on is the first part of the command, 1 bit (1 or 0)
		X dimention (x10) is the second part of the command, 9 bits (0 to 511)
		Y dimention (x10) is the third part of the command, 9 bits (0 to 511)

		Example G01 X25.4 Y10.8

		G01 = 1
		X25.4 = 254 = 011111110 (remember we are using 9 bits)
		Y10.8 = 108 = 001101100 (remember we are using 9 bits)

		we put them into a 24 bit command
		000001011111110001101100 (5 bits are not used, so it will alwas start with 00000)

		= 392300 (this number can be held in 3 Bytes)

		When plotting this code we just do a revers convertion to a standard G-Code.

		By doing this we have reduced a command by 80%
		So we can fit 80% more plot commands on the memory.

		Lets say we take some for menue and plot names:
		Lets 500 bytes for menu names.
		Lets 500 bytes for Plot names. Plot names to be 10 charectors long (use spaces to extend). this gives room for 50 plot names.
		Leaving 31k byte for plots.

		So 31000/3 = 10333 plot commands.

		If I add more memory IC, each extra will have 32000/3 = 10666 plot commands.

		decided to use 2 of the spair bits to indicate start and end of a plot

		NOTE! Arduino does not recognize sent exstended ASCII, so send raw bits.

	*/


	/*	===		EEPROM Checks	===	*/

	readWords_Mini_Plotter_2();	/*	512 I2C EEPROM	1	*/
	//ReadCharectors();				/*	512 I2C EEPROM	3	*/

	/*	===		Workings	===	*/

	//ClearMemory(0, 1000);
	//ReadMemory(0, 900);

	//MemTest32KB(0, 499, 32);

	//writeMenuData();
	//writePlotNames();
	//readWords_Cybot_IR();
	//ReadPlotFiles_Mem_1();
	//ReadPlotFiles_Mem_2();
	//ReadPlotFiles_Mem_1_compressed(3000, 156);/*	 cube				*/
	//ReadPlotFiles_Mem_1_compressed(3157, 606);/*	 snowflake			*/
	//ReadPlotFiles_Mem_1_compressed(1296, 150);
	//ReadPlotFiles_Mem_1_compressed(4831, 615);/*	 Witch on a stick	*/
	//printStringArrays();


}

void loop()
{
	Serial.flush();

	if (!procsessingString) {
		ReadSerial();

	}



}
void ReadSerial() {

	char p;
	char c;
	/*	Read characters if we have them.	*/
	if (Serial.available() > 0) {
		no_data = 0;
		p = Serial.peek();
		c = Serial.read();
		/*	Newlines are ends of commands.	*/
		if (!(c == '\r' && p == '\n') || sofar <= lengthOfData) {

			buffer[sofar] = c;
			sofar++;
		}
	}
	else {

		/*	If data count is grater than Zero AND eather char is a Carage Return, char is a New Line or Timed Out.	*/
		if (sofar && (c == '\n' || c == '\r' || no_data > 100)) {

			while (sofar < MAX_BUF) {
				c = Serial.read();
				buffer[sofar] = 0;
				sofar++;
			}

			if (*buffer != '\n' && *buffer != '\r') {

				procsessingString = true;
				if (*buffer == '$' && buffer[1] == 's') { changeSettings(); }
				else { writeCommand(); }

			}
			delay(30);
			init_process_string();	/*	Clear Command.	*/
		}
		no_data++;
	}
}
void init_process_string() {

	/*
		Init our command.
		Clean buffer and send ready "ok".
	*/
	for (byte i = 0; i < MAX_BUF; i++) { buffer[i] = 0; }
	sofar = 0;
	no_data = 0;
	Serial.println("ok");
	delay(20);
	Serial.flush();
	procsessingString = false;
}
void writeCommand() {

	//Serial.print("Writing Command. Data Length ");	/*	 don't use unless needed	*/
	//delay(20);
	//Serial.println(lengthOfData);	/*	 don't use unless needed	*/
	//delay(20);

	delay(30);

	for (byte i = 0; i < lengthOfData; i++) {

		Wire.beginTransmission(EEPROM_ADD);
		delay(2);
		Wire.write((int)(dataStartAddress >> 8));
		delay(6);
		Wire.write((int)(dataStartAddress & 0xFF));
		delay(6);

		Wire.write(byte(buffer[i]));
		delay(6);

		Wire.endTransmission();
		delay(2);

		dataStartAddress++;


	}

	delay(40);
	//Serial.print("Command Written");	/*	 Don't use unless needed.	*/
	//delay(20);

}
void changeSettings() {

	delay(30);

	char* ptr = buffer;				/*	 Start at the beginning of buffer.							*/

	ptr = strchr(ptr, ' ') + 1;		/*	 Take a step from here to the char. after the next space.	*/
	dataStartAddress = atof(ptr);

	ptr = strchr(ptr, ' ') + 1;		/*	 Take a step from here to the char. after the next space.	*/
	lengthOfData = atof(ptr);

	Serial.print("Start Address: ");
	delay(20);
	Serial.println(dataStartAddress);
	delay(20);
	//Serial.flush();
	Serial.print("Page Length: ");
	delay(20);
	Serial.println(lengthOfData);
	delay(20);
	//Serial.flush();

}

	/*	===		Workings	===	*/
void printStringArrays() {

	for (size_t i = 0; i < menuWordsLength; i++) {

		Serial.println(menuWords[i]);
		Serial.flush();

	}

	for (size_t i = 0; i < plotNamesLength; i++) {

		Serial.println(plotNames[i]);
		Serial.flush();

	}


}
void readWords_Mini_Plotter_2() {

	Serial.println();
	Serial.println();
	Serial.flush();

	/*	Menu :	*/
	readWord(0, 4);		/*	1 MAIN						*/
	readWord(4, 11);	/*	2 MANUAL DRAW				*/
	readWord(15, 11);	/*	3 CHOOSE PLOT				*/
	readWord(26, 8);	/*	4 SETTINGS					*/
	readWord(34, 4);	/*	5 INFO						*/
	readWord(38, 5);	/*	6 RESET						*/
	readWord(43, 6);	/*	7 MOVE X					*/
	readWord(49, 6);	/*	8 DRAW X					*/
	readWord(55, 6);	/*	9 MOVE Y					*/
	readWord(61, 6);	/*	10 DRAW Y					*/
	readWord(67, 9);	/*	11 <<= = BACK				*/
	readWord(76, 5);	/*	12 SPEED					*/
	readWord(81, 4);	/*	13 TOOL						*/
	readWord(85, 2);	/*	14 --						*/
	readWord(87, 18);	/*	15 Tim's Mini Plotter		*/
	readWord(105, 2);	/*	16 ok						*/
	readWord(107, 18);	/*	17 == = Motors Off == =		*/
	readWord(125, 9);	/*	18 Version:					*/
	readWord(134, 20);	/*	19 Basic Gcode Commands		*/
	readWord(154, 18);	/*	20 M03 - Tool On/Down		*/
	readWord(172, 17);	/*	21 M05 - Tool Off/Up		*/
	readWord(189, 16);	/*	22 M18 - Motors Off			*/
	readWord(205, 12);	/*	23 System Reset				*/
	readWord(217, 24);	/*	24 M100 - this Info message	*/
	readWord(241, 19);	/*	25 R01 - Reset Plotter		*/
	readWord(260, 19);	/*	26 By Tim Jackson.1960		*/
	readWord(279, 16);	/*	27 ================			*/
	readWord(295, 10);	/*	28 (10 spaces)				*/
	readWord(305, 12);	/*	29 TYPE OF PLOT				*/
	readWord(317, 7);	/*	30 OUTLINE					*/
	readWord(324, 4);	/*	31 TEXT						*/
	readWord(328, 14);	/*	32 CHOOSE OUTLINE			*/
	readWord(342, 3);	/*	33 A - Z					*/
	readWord(345, 3);	/*	34 a - z					*/
	readWord(348, 3);	/*	35 0 - 9					*/
	readWord(351, 7);	/*	36 SYMBOLS					*/
	readWord(358, 10);	/*	37 CHOOSE A - Z				*/
	readWord(368, 10);	/*	38 CHOOSE a - z				*/
	readWord(378, 10);	/*	39 CHOOSE 0 - 9				*/
	readWord(388, 14);	/*	40 CHOOSE SYMBOLS			*/
	readWord(402, 16);	/*	41 CHOOSE CHARACTER			*/
	readWord(418, 5);	/*	42 Servo					*/
	readWord(423, 5);	/*	42 Laser					*/
	readWord(428, 6);	/*	42 EndEND					*/

	Serial.println();
	Serial.println();
	Serial.flush();

	/*	Number of plots	*/
	readWord(2991, 1);					/*	char of byte number of plots.	*/
	Serial.print("Number of plots = ");
	Serial.println(memNumber);			/*	byte number of plots.			*/
	Serial.flush();


	/*	 Plot Names + location:	*/
	Serial.println();
	Serial.println("=== Plot List ===");
	Serial.println();



	//for (size_t i = 500; i < 3000; i += 15) {	/*	 all	*/
	for (size_t i = 500; i < int(500 + ((memNumber - 1) * 15)); i += 15) {

		readPlotNames(i);

	}




}
void readWords_Cybot_IR() {

	Serial.println();
	Serial.println();
	Serial.flush();

	/*	Menu Words:	*/

	readWord(0, 10);	/*	<10 Spaces>				*/
	readWord(10, 5);	/*	GAMES					*/
	readWord(15, 5);	/*	CYBOT					*/
	readWord(15, 13);	/*	CYBOT TRAINER			*/
	readWord(28, 11);	/*	CYBOT RACER				*/
	readWord(39, 8);	/*	MUNCHBOT				*/
	readWord(47, 5);	/*	ROBOT					*/
	readWord(47, 12);	/*	ROBOT SELECT			*/
	readWord(59, 4);	/*	MODE					*/
	readWord(63, 7);	/*	PC LINK					*/
	readWord(70, 5);	/*	RESET					*/
	readWord(75, 5);	/*	Cybot					*/
	readWord(80, 3);	/*	Tom						*/
	readWord(83, 7);	/*	ROBOT 3					*/
	readWord(90, 9);	/*	<<== Back				*/
	readWord(99, 13);	/*	CYBOT CHANNEL			*/
	readWord(112, 3);	/*	TOM						*/
	readWord(112, 11);	/*	TOM CHANNEL				*/
	readWord(123, 5);	/*	SONAR					*/
	readWord(123, 8);	/*	SONAR(T)				*/
	readWord(131, 5);	/*	LIGHT					*/
	readWord(136, 11);	/*	FOLLOW LINE				*/
	readWord(147, 14);	/*	REMOTE CONTROL			*/
	readWord(147, 17);	/*	REMOTE CONTROL(T)		*/
	readWord(164, 14);	/*	RUN PROGRAM(T)			*/
	readWord(178, 15);	/*	TRACK IR TAG(T)			*/
	readWord(193, 6);	/*	CYBALL					*/
	readWord(199, 2);	/*	AI						*/
	readWord(201, 13);	/*	HIDE AND SEEK			*/
	readWord(214, 10);	/*	AVOID FAST				*/
	readWord(214, 13);	/*	AVOID FAST(T)			*/
	readWord(227, 10);	/*	AVOID SLOW				*/
	readWord(237, 6);	/*	FOLLOW					*/
	readWord(237, 9);	/*	FOLLOW(T)				*/
	readWord(246, 11);	/*	FOLLOW FAST				*/
	readWord(257, 11);	/*	FOLLOW SLOW				*/
	readWord(268, 5);	/*	SETUP					*/
	readWord(268, 8);	/*	SETUP(T)				*/
	readWord(276, 9);	/*	ACTIVATED				*/
	readWord(285, 8);	/*	BUTTON A				*/
	readWord(293, 8);	/*	BUTTON B				*/
	readWord(301, 8);	/*	BUTTON C				*/
	readWord(309, 8);	/*	BUTTON D				*/
	readWord(317, 14);	/*	FLASH AMTENNAE			*/
	readWord(331, 13);	/*	FLASH LEDS(T)			*/
	readWord(344, 15);	/*	AMTENNAE ON/OFF			*/
	readWord(359, 14);	/*	LEDS ON/OFF(T)			*/
	readWord(373, 13);	/*	BEEP(T)/SHOOT			*/
	readWord(386, 8);	/*	CHIME(T)				*/
	readWord(394, 8);	/*	AUDIO(T)				*/
	readWord(402, 12);	/*	RECORD SOUND			*/
	readWord(414, 8);	/*	DOWNLOAD				*/
	readWord(422, 12);	/*	CLEAR MEMORY			*/
	readWord(434, 15);	/*	PLAY FLASH FILE			*/
	readWord(449, 20);	/*	VOICE RECOGNITION(T)	*/
	readWord(469, 21);	/*	SETUP USER COMMAND(T)	*/
	readWord(490, 7);	/*	LIBRARY					*/
	readWord(497, 6);	/*	YES/NO					*/
	readWord(503, 14);	/*	03/04/VR ON(T)			*/
	readWord(517, 17);	/*	03/04 ACTIVATE(T)		*/
	readWord(523, 11);	/*	ACTIVATE(T)				*/
	readWord(534, 10);	/*	PROGRAM 01				*/
	readWord(544, 10);	/*	PROGRAM 02				*/
	readWord(554, 16);	/*	1 PLAYER (CYBOT)		*/
	readWord(570, 16);	/*	2 PLAYER (CYBOT)		*/
	readWord(586, 14);	/*	1 PLAYER (TOM)			*/
	readWord(600, 20);	/*	TOM VS CYBOT (SMART)	*/
	readWord(620, 8);	/*	4 PLAYER				*/
	readWord(628, 12);	/*	UNSUPERVISED			*/
	readWord(640, 10);	/*	SUPERVISED				*/
	readWord(650, 11);	/*	CYBOT SEEKS				*/
	readWord(661, 9);	/*	TOM SEEKS				*/
	readWord(670, 4);	/*	<==>					*/
	readWord(674, 3);	/*	USB						*/
	readWord(677, 1);	/*	-						*/



	Serial.println();
	Serial.println();
	Serial.flush();

	/*	Plot Names + location:	*/

	////for (size_t i = 500; i < 3000; i += 15) {	/*	all	*/
	//for (size_t i = 500; i < 770; i += 15) {

	//	readPlotNames(i);


	//}

	//readWord(2991, 1);			/*	char of byte number of plots	*/
	//Serial.println(memNumber);	/*	 byte number of plots			*/
	//Serial.flush();



}
void ReadCharectors() {

	/*	 Charector Plots Stored on EEPROM 3	*/

	Serial.println();
	Serial.println();
	Serial.flush();

	/*	 Plot Charectors + location:	*/

	//for (size_t i = 0; i < (52 * 6); i += 6) {	/*	 all	*/
	for (size_t i = 0; i < (88 * 6); i += 6) {

		readPlotCharectors(i);

	}

}
void ReadPlotFiles_Mem_1() {

	/*
		To Write file:
		Set dataStartAddress to Start Address
		File lenth is determined by File Sender

		To read file:
		Use command:
		readCommand(dataStartAddress, Length of file commands);
		ie. readCommand(1000, 238);

	*/

	//readWord(1000, 15);	/*	start address, number of bytes	*/
	//readWord(1015, 15);	/*	start address, number of bytes	*/
	//readWord(1030, 15);	/*	start address, number of bytes	*/
	//readWord(1045, 15);	/*	start address, number of bytes	*/
	//readWord(1060, 15);	/*	start address, number of bytes	*/
	//readWord(1075, 15);	/*	start address, number of bytes	*/
	//readWord(1090, 15);	/*	start address, number of bytes	*/
	//readWord(1105, 15);	/*	start address, number of bytes	*/
	//readWord(1120, 15);	/*	start address, number of bytes	*/
	//readWord(1135, 15);	/*	start address, number of bytes	*/
	//readWord(1150, 15);	/*	start address, number of bytes	*/
	//readWord(1165, 15);	/*	start address, number of bytes	*/
	//readWord(1180, 15);	/*	start address, number of bytes	*/
	//readWord(1195, 15);	/*	start address, number of bytes	*/
	//readWord(1210, 15);	/*	start address, number of bytes	*/
	//readWord(1225, 15);	/*	start address, number of bytes	*/
	//readWord(1240, 15);	/*	start address, number of bytes	*/



	/*	 ALL (Cube","Snowflake", "Wolf", "Links","Witch","Unicorn 1" ,"Butterfly", "Spider" ,"Triangles")	*/
	//readCommand(1000, 20);	/*	(1000,2066)	*/


	/*	Cube	*/
	Serial.println();
	Serial.println("Cube");
	Serial.println();
	Serial.flush();
	readCommand(1015, 6);

	/*	Snowflake	*/
	Serial.println();
	Serial.println("Snowflake");
	Serial.println();
	Serial.flush();
	readCommand(2230, 6);

	/*	Wolf Howling	*/
	Serial.println();
	Serial.println("Wolf Howling");
	Serial.println();
	Serial.flush();
	readCommand(5725, 6);

	/*	Links	*/
	Serial.println();
	Serial.println("Links");
	Serial.println();
	Serial.flush();
	readCommand(8890, 6);

	/*	Witch on a Stick	*/
	Serial.println();
	Serial.println("Witch on a Stick");
	Serial.println();
	Serial.flush();
	readCommand(12280, 6);

	/*	Unicorn 1	*/
	Serial.println();
	Serial.println("Unicorn 1");
	Serial.println();
	Serial.flush();
	readCommand(15820, 6);

	/*	Butterfly	*/
	Serial.println();
	Serial.println("Butterfly");
	Serial.println();
	Serial.flush();
	readCommand(19900, 6);

	/*	Spider	*/
	Serial.println();
	Serial.println("Spider");
	Serial.println();
	Serial.flush();
	readCommand(24745, 6);

	/*	Rotating Triangles	*/
	Serial.println();
	Serial.println("Rotating Triangles");
	Serial.println();
	Serial.flush();
	readCommand(29080, 6);



}
void ReadPlotFiles_Mem_2() {

	/*
		To Write file:
		Set dataStartAddress to Start Address
		File lenth is determined by File Sender

		To read file:
		Use command:
		readCommand(dataStartAddress, Length of file commands);
		ie. readCommand(1000, 238);

	*/

	/*
		"Skull"			515		15
		"Tim"			544		7710
		"Alien"			129		15870
		"Agent"			348		17805
		"5 P Star"		15		23025
		"9 P Star"		23		23250
		"18 P Star"		41		23595
		"Reaper"		145		24210
		"Octopus"		367		26385

	*/

	/*	 ALL ("Skull","Tim", "Alien", "Agent", "5 P Star", "9 P Star", "18 P Star", "Reaper", "Octopus")	*/
	//delay(100);
	//readCommand(0, 2133);

	/*	"Skull"	*/
	Serial.println();
	Serial.println("Skull");
	Serial.println();
	Serial.flush();
	readCommand(15, 6);
	//readCommand(15, 515);


	/*	 "Tim"	*/
	Serial.println();
	Serial.println("Tim");
	Serial.println();
	Serial.flush();
	readCommand(7710, 6);
	//readCommand(7710, 544);

	/*	 "Alien"	*/
	Serial.println();
	Serial.println("Alien");
	Serial.println();
	Serial.flush();
	readCommand(15870, 6);
	//readCommand(15870, 129);

	/*	 "Agent"	*/
	Serial.println();
	Serial.println("Agent");
	Serial.println();
	Serial.flush();
	readCommand(17805, 6);
	//readCommand(17805, 348);

	/*	 "5 P Star"	*/
	Serial.println();
	Serial.println("5 P Star");
	Serial.println();
	Serial.flush();
	readCommand(23025, 6);
	//readCommand(23025, 15);

	/*	 "9 P Star"	*/
	Serial.println();
	Serial.println("9 P Star");
	Serial.println();
	Serial.flush();
	readCommand(23250, 6);
	//readCommand(23250, 23);

	/*	 "18 P Star"	*/
	Serial.println();
	Serial.println("18 P Star");
	Serial.println();
	Serial.flush();
	readCommand(23595, 6);
	//readCommand(23595, 41);

	/*	 "Reaper"	*/
	Serial.println();
	Serial.println("Reaper");
	Serial.println();
	Serial.flush();
	readCommand(24210, 6);
	//readCommand(24210, 145);

	/*	 "Octopus"	*/
	Serial.println();
	Serial.println("Octopus");
	Serial.println();
	Serial.flush();
	readCommand(26385, 6);
	//readCommand(26385, 367);


}
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

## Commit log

2024-08-06 Initial Publish
    [0.dxf, 1.dxf, 2.dxf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]
2024-08-06 Add STL Files
    [Holding_Screw.stl, Knob.stl, OLED_Support.stl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]
2025-02-20 Added FreeCAD Files
    [Part Z.FCStd]
2025-03-22 Added AVRDUDE
    [Mini Plotter 2 Full.kicad_sch]
